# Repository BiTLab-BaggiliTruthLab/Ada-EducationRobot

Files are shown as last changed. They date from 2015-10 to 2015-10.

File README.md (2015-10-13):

# Ada-EducationRobot
######Ada the Cyber Security Awareness Robot
---
<a href="http://www.youtube.com/watch?feature=player_embedded&v=IIVzHWTThcU
" target="_blank">Ada The Cyber Security Education Robot</a>

## Building Instructions
---
###Hardware
Hardware building instructions can be found in our <a href="http://www.unhcfreg.com/#!Ada-The-Cyber-Security-Education-Robot/c5rt/561c4c410cf297bd6860a78e">blog post</a>

###Software
The code for the master and slave applications can be found in /Ada-EducationRobot/SecuroBotMaster and /Ada-EducationRobot/SecuroBotSlave, respectively. These folders can be imported into Android Studio. Android Studio is a free program that can be downloaded <a
href="http://developer.android.com/sdk/index.html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">here</a>.

The Arduino code can be found in /Ada-EducationRobot/SecuroBotServo/SecuroBotServo.ino. This code can be opened in the Arduino IDE, downloadable from <a
href="https://www.arduino.cc/en/Main/Software">here</a>.

##Contact
##### Made by Devon Clark
dclar4@unh.newhaven.edu

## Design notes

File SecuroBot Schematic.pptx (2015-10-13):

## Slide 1

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
TIP31

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
Slave
Audio
Out

L

R

●

+
LM324

GND

V+

47kΩ

+5V

IR Sen.

SIG

GND

4.7kΩ

●

●

●

●

+5V

Servo

GND

SIG

G5V-2-H1 5V Relay

●

●

330Ω

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
Master Tablet USB

Vcc

GND

●

D+

D-

Slave Tablet USB

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
LM7805

3

2

●

1

LM7805

3

2

1

LM7805

3

2

Android IOIO

13

9

1N4007

●

●

1N4007

●

●

●

VIN

GND

+5V

0 (Rx)

Arduino

7

9

7.4VDC
5000mAh

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
LEADS

VIN

●

●

●

1N4007

●

●

●

1N4007

●

●

●

●

GND

●

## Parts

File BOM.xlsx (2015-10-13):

Description | Pkg QTY | QTY of Pkgs | Used QTY | Pkg Cost | Unit Cost | Used Cost | Link
Battery | 1 | 2 | 2 | $18.40 | $18.40 | $36.80 | http://www.ebay.com/itm/RC-Turnigy-5000mAh-2S-20C-Lipo-Pack-/261569382452?pt=LH_DefaultDomain_0
IR prox sensors (5V) w/cable | 1 | 1 | 1 | $13.95 | $13.95 | $13.95 | http://www.ebay.com/itm/1x-Sharp-GP2Y0A21YK0F-Infrared-IR-Distance-Sensor-10-80cm-/141429691827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
Android IOIO OTG (5-15V) | 1 | 1 | 1 | $39.95 | $39.95 | $39.95 | http://www.ebay.com/itm/SparkFun-IOIO-OTG-/191528032653?pt=LH_DefaultDomain_0&hash=item2c97f5d98d
90 deg audio cable - 4ft | 1 | 1 | 1 | $4.68 | $4.68 | $4.68 | http://www.ebay.com/itm/Sirius-XM-3-5mm-male-to-male-Auxiliary-Audio-Cable-Right-Angle-90-degrees-10065x-/221586020592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
90 deg micro USB cable | 1 | 2 | 2 | $2.39 | $2.39 | $4.78 | http://www.ebay.com/itm/StarTech-com-Micro-USB-Cable-A-to-Right-Angle-Micro-B-UUSBHAUB3RA-New-/281528968323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
amplified speaker system (5V) | 1 | 1 | 1 | $16.95 | $16.95 | $16.95 | http://www.ebay.com/itm/Frisby-Desktop-Laptop-Notebook-Computer-PC-Mini-USB-Powered-Portable-Speakers-/131376665293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
Standard Servo (5V) | 1 | 1 | 1 | $14.99 | $14.99 | $14.99 | http://www.radioshack.com/radioshack-standard-servo/2730766.html
Servo driven rotating base | 1 | 1 | 1 | 19.95 | $19.95 | $19.95 | http://www.robotshop.com/en/lynxmotion-base-rotate-kit-no-servo.html
5mm Blue LED | 1 | 12 | 12 | $0.49 | $0.49 | $5.88 | http://www.ledsupply.com/leds/5mm-led-blue-470nm-30-degree-viewing-angle
USB BLE transeiver (non hub) | 1 | 1 | 1 | $4.99 | $4.99 | $4.99 | http://www.dx.com/p/ultra-mini-bluetooth-3-0-usb-dongle-65631#.VhaAQflVhBc
proto board | 1 | 1 | 1 | $19.95 | $19.95 | $19.95 | http://www.adafruit.com/products/590
9 pin screw terminal | 1 | 3 | 3 | $3.05 | $3.05 | $9.15 | http://www.adafruit.com/product/2134
Arduino Uno | 1 | 1 | 1 | $24.95 | $24.95 | $24.95 | http://www.adafruit.com/product/50
SKYRC iMAX B6AC V2 battery charger | 1 | 1 | 1 | 55.99 | $55.99 | $55.99 | http://www.amazon.com/Genuine-SKYRC-Power-6Amps-50Watts/dp/B00ND7J38C
3 pin JST-XH balancer connectors | 10 | 1 | 1 | $2.74 | 0.274 | $0.27 | http://www.amazon.com/10pcs-JST-XH-Lipo-Balance-Extension/dp/B008TKMC86
male/female T style connectors | 10 | 1 | 1 | $3.10 | $0.31 | $0.31 | http://www.amazon.com/gp/product/B0070RS7V0?redirect=true
Battery socket and pin pair | 2 | 1 | 1 | $4.55 | $2.27 | $2.27 | http://www.amazon.com/Redcat-Racing-Banana-Version-Female/dp/B00D25G2HA
5V Voltage regulator LM1085 | 1 | 2 | 2 | $2.06 | $2.06 | $4.12 | http://www.mouser.com/ProductDetail/Texas-Instruments/LM1085IT-ADJ-NOPB/?qs=sGAEpiMZZMvu8NZDyZ4K0VV0B0ysNg0m
LM324 Quad Opperational Amplifier | 1 | 1 | 1 | $0.51 | $0.51 | $0.51 | http://www.mouser.com/ProductDetail/Fairchild-Semiconductor/LM324N/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
TIP31 NPN Transistor | 1 | 1 | 1 | $1.13 | $1.13 | $1.13 | http://www.mouser.com/ProductDetail/Central-Semiconductor/TIP31/?qs=sGAEpiMZZMutncetXCRkfnN4f3PuPq4Y
4.7kΩ Resistor | 1 | 1 | 1 | $0.70 | $0.70 | $0.70 | http://www.mouser.com/ProductDetail/Ohmite/OD472JE/?qs=sGAEpiMZZMuDPtTs5Gda20wkUEoAUy6cJVhknFF6uiU%3d
47kΩ Resistor | 1 | 1 | 1 | $0.70 | $0.70 | $0.70 | http://www.mouser.com/ProductDetail/Ohmite/OD473JE/?qs=sGAEpiMZZMuDPtTs5Gda2xA0s8Om0erSLiRj1MkjNK8%3d
330Ω Resistor | 1 | 1 | 1 | $0.70 | $0.70 | $0.70 | http://www.mouser.com/ProductDetail/Ohmite/OD331JE/?qs=sGAEpiMZZMuDPtTs5Gda29oHdSiM7txmqu9ayzW2Kb0%3d
G5V-2-H1 5V Relay | 1 | 1 | 1 | $2.99 | $2.99 | $2.99 | http://www.mouser.com/ProductDetail/Omron-Electronics/G5V-2-H1-DC5/
DPST toggle switch (center off) | 1 | 1 | 1 | $5.99 | $5.99 | $5.99 | http://www.mouser.com/ProductDetail/NKK-Switches/S7A/
heat sink | 1 | 2 | 2 | $0.51 | $0.51 | $1.02 | http://www.mouser.com/ProductDetail/Aavid-Thermalloy/576802B04000G/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
1N4007 Diode | 1 | 2 | 2 | $0.18 | $0.18 | $0.36 | http://www.mouser.com/ProductDetail/Fairchild-Semiconductor/1N4007/?qs=sGAEpiMZZMuQUXCJI7Y4lvWy%252b1U8RtCq
*80/20 1.5in. solid extrusion - 8ft | 1 | 2 | 1.5 | $61.31 | $61.31 | $91.97 | http://www.mcmaster.com/#47065t103/=wu75em
80/20 1.5in 90 deg corner | 1 | 0 | 0 | $7.84 | $7.84 | $0.00 | http://www.mcmaster.com/#47065t243/=wu7542
80/20 1.5in 90 deg brace | 1 | 5 | 5 | $7.98 | $7.98 | $39.90 | http://www.mcmaster.com/#5537t51/=wu75yk
grey wire track snap (6ft length) | 1 | 1 | 1 | $4.27 | $4.27 | $4.27 | http://www.mcmaster.com/#47065t4/=z9058j
5/16 Aluminum washers | 100 | 1 | 22 | $7.88 | $0.08 | $1.73 | http://www.mcmaster.com/#93286a015/=z945r5
7" x 5" x 2.5" Electrical enclosure | 1 | 1 | 1 | $12.20 | $12.20 | $12.20 | http://www.mcmaster.com/#7593k32/=z90j3c
80/20 T-slot fastener for 1.5 in. extrusion | 4 | 5 | 18 | $2.71 | $0.68 | $12.20 | http://www.mcmaster.com/#47065t97/=z621i9
1.75 X 5/16-18 socket head cap screw | 2 | 1 | 2 | $2.10 | $1.05 | $2.10 | http://www.homedepot.com/p/Crown-Bolt-5-16-in-x-1-3-4-in-Internal-Hex-Socket-Cap-Head-Cap-Screws-2-Pack-45338/203576071
5/16 - 18 1.25 in. bolt | 1 | 2 | 2 | $0.20 | $0.20 | $0.40 | http://www.lowes.com/pd_63318-37672-190096_1z0v10o__?productId=3058581&pl=1
1/2in conduit strain relief | 1 | 3 | 3 | $3.04 | $3.04 | $9.12 | http://www.lowes.com/pd_108659-15527-49212___?productId=3150213&pl=1&Ntt=gampak+flex+connector
1/2in conduit lock nut | 2 | 2 | 3 | $1.50 | $0.75 | $2.25 | http://www.lowes.com/pd_75927-15527-47106_1z0xc72__?productId=1100417&pl=1
#6-32 X 1.5 in. machine screw/nut | 10 | 1 | 2 | $1.24 | $0.12 | $0.25 | http://www.lowes.com/ProductDisplay?productId=3035920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
.25x.14x1 in. nylon spacers | 2 | 1 | 2 | $0.56 | $0.28 | $0.56 | http://www.lowes.com/pd_136921-37672-880429_0__?productId=3012432
#6-32 x 1.25 machine screw/nut | 10 | 1 | 8 | $1.24 | $0.12 | $0.99 | http://www.lowes.com/pd_57834-37672-605399___?productId=4746423&pl=1&Ntt=57834
#4-40 x 0.5in machine screw | 8 | 1 | 6 | $1.24 | $0.15 | $0.93 | http://www.lowes.com/pd_62179-37672-605438_0__?productId=4746589
2" grey swivel wheel w/lock | 1 | 4 | 4 | $4.97 | $4.97 | $19.88 | http://www.lowes.com/pd_235514-255-4031299NN_0__?productId=3026956
5/16 lock washers | 1 | 20 | 20 | $0.18 | $0.18 | $3.60 | http://www.lowes.com/pd_63409-37672-300021___?productId=3036826&pl=1&Ntt=5%2F16+lock+washer
3/8 lock washer | 1 | 4 | 4 | $0.23 | $0.23 | $0.92 | http://www.lowes.com/pd_61816-37672-811056___?productId=3036632&pl=1&Ntt=3%2F8+lock+washer
3/8 - 16 nut | 1 | 8 | 8 | $0.22 | $0.22 | $1.76 | http://www.lowes.com/pd_63303-37672-150009_4294856646+5003696+4294838133_4294937087?productId=3058551
#10-32 X 1/2" machine screw w/ nut | 10 | 1 | 3 | $1.24 | $0.12 | $0.37 | http://www.lowes.com/pd_57851-37672-491306___?productId=3035878&pl=1&Ntt=%2310-32+x+1%2F2
#10 lock washer | 48 | 1 | 3 | $1.24 | $0.03 | $0.08 | http://www.lowes.com/pd_58135-37672-490694___?productId=3035994&pl=1&Ntt=%2310+lock+washer
#6 x 0.5-in Stainless Steel Screws | 12 | 1 | 8 | $1.54 | $0.13 | $1.03 | http://www.lowes.com/pd_329037-37672-126976___?Ntt=126976&UserSearch=126976&productId=3818121
Nexus 7 tablet | 1 | 2 | 2 | 149 | $149.00 | $298.00 | http://www.newegg.com/Product/Product.aspx?Item=N82E16834231150&cm_re=nexus_7-_-34-231-150-_-Product
 |  |  |  |  | Total: | $798.54 | *This does not include the cost of filiment for 3D printing or wire

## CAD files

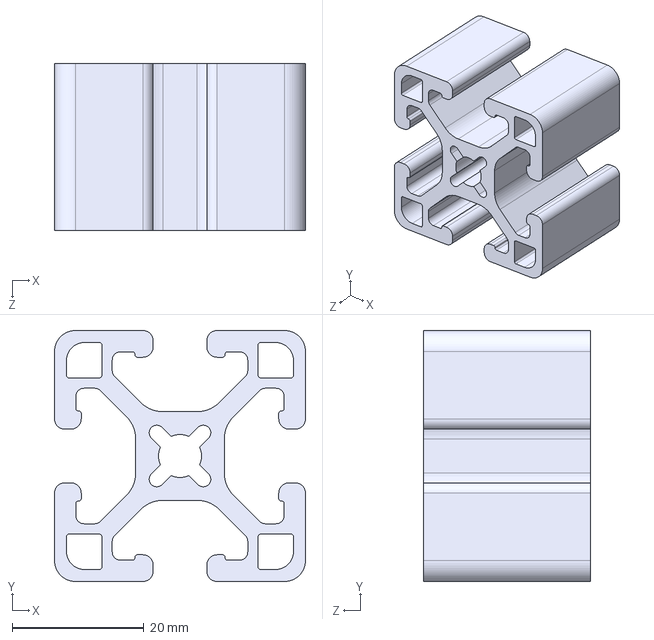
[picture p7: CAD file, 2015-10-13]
SecuroBot Hardware Files/CAD Files/Imported Components/8020 - extrusion - 1 inch/1 inch extrusion base.step
38.1 x 38.1 x 25.4 mm

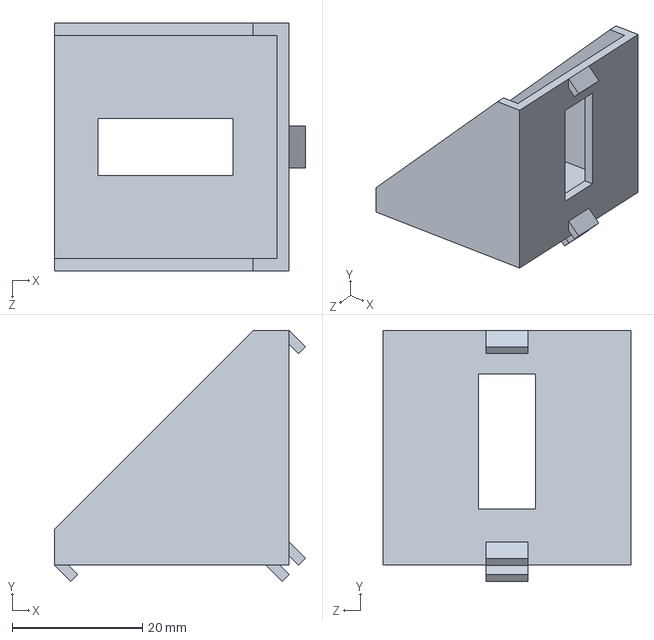
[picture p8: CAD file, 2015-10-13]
SecuroBot Hardware Files/CAD Files/Imported Components/ANGLE BRACE/ANGLE BRACE.STEP
38.5 x 38.5 x 38.0 mm

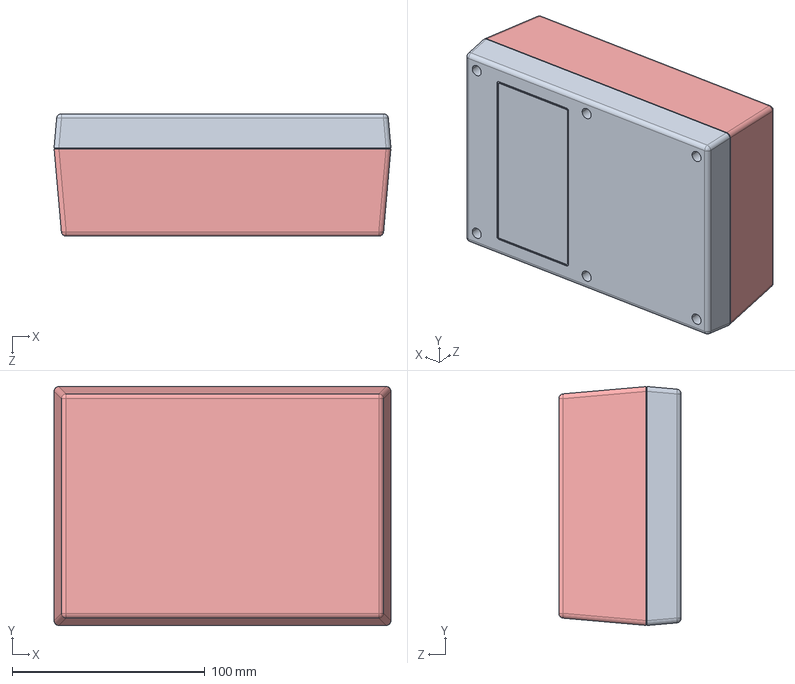
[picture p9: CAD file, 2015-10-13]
SecuroBot Hardware Files/CAD Files/Imported Components/enclosure/enclosure.STEP
174.8 x 124.0 x 63.5 mm

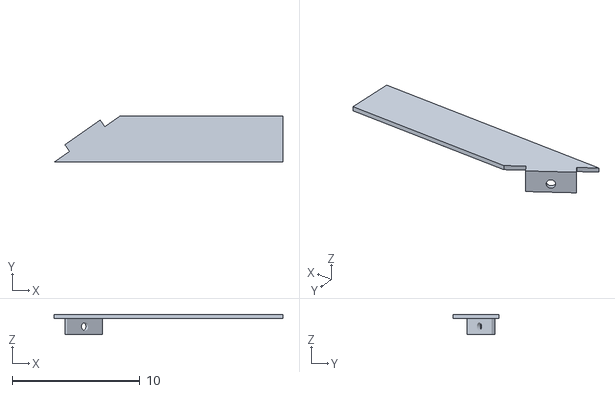
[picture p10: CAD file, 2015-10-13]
SecuroBot Hardware Files/STL Files/Right Forearm.stl
17.9 x 3.64 x 1.59

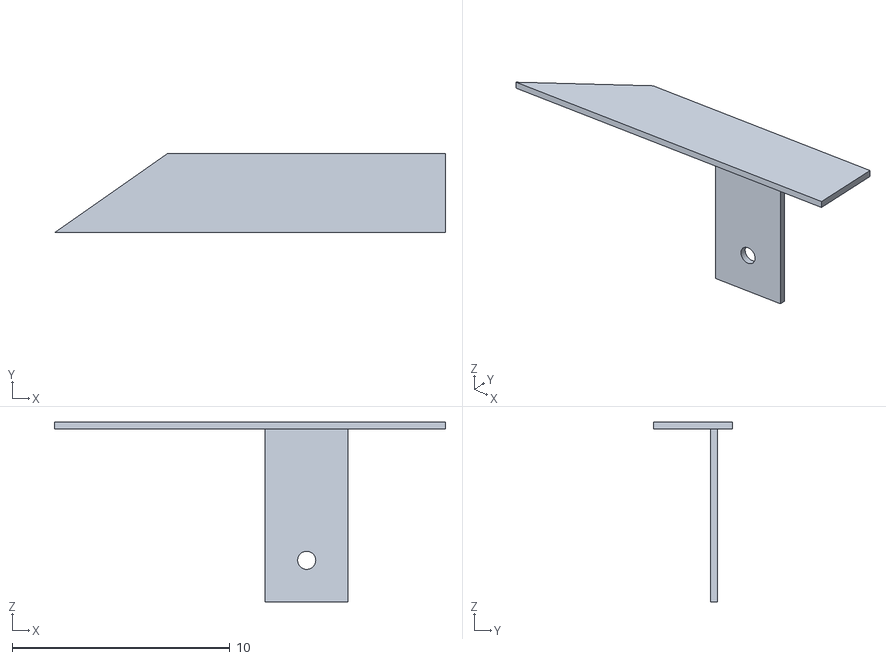
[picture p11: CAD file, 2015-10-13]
SecuroBot Hardware Files/STL Files/Left Forearm.stl
17.9 x 3.64 x 8.24

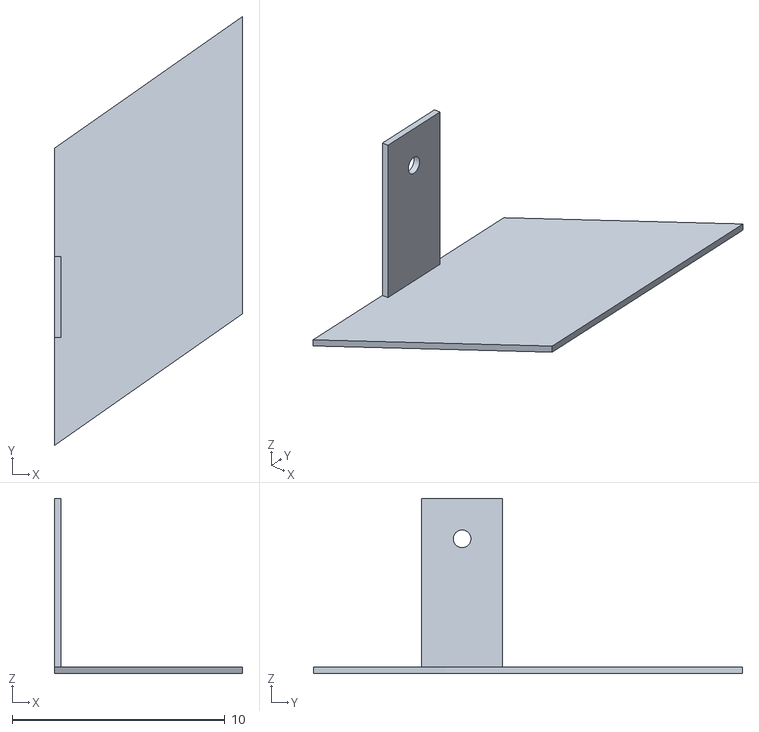
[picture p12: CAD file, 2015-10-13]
SecuroBot Hardware Files/STL Files/Right Abdomen.stl
8.84 x 20.2 x 8.24

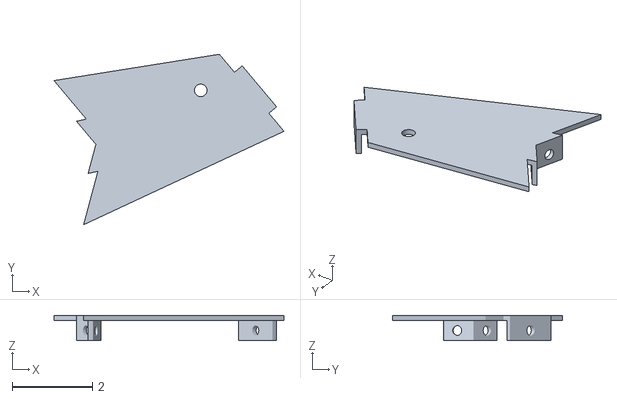
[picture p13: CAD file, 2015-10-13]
SecuroBot Hardware Files/STL Files/Right Bicep.stl
5.72 x 4.24 x 0.625

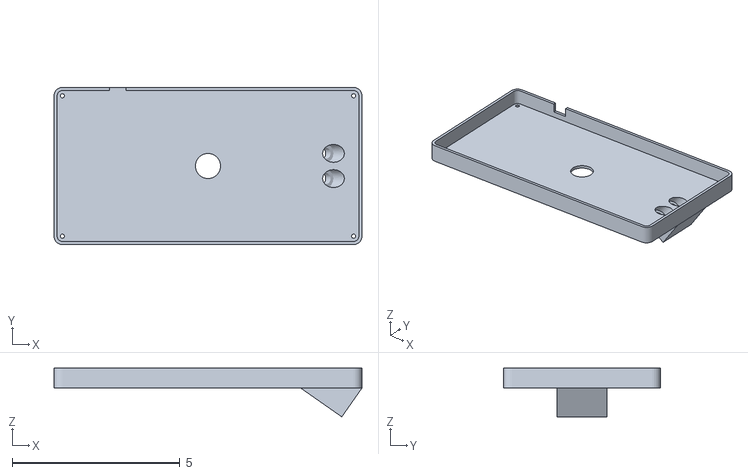
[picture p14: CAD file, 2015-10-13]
SecuroBot Hardware Files/STL Files/Slave Tablet Enclosure.stl
9.19 x 4.69 x 1.45

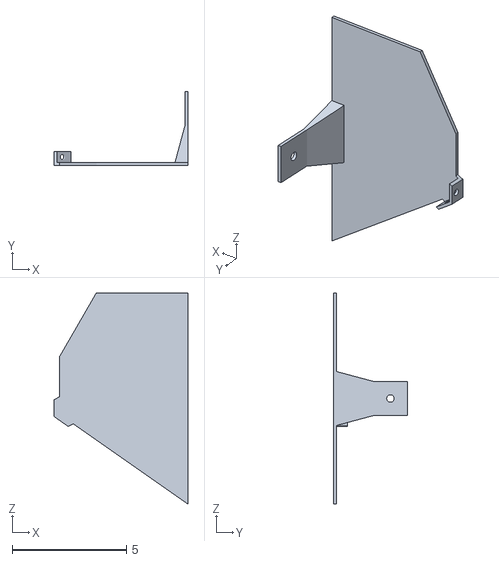
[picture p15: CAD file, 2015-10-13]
SecuroBot Hardware Files/STL Files/Right Chest.stl
5.85 x 3.25 x 9.25

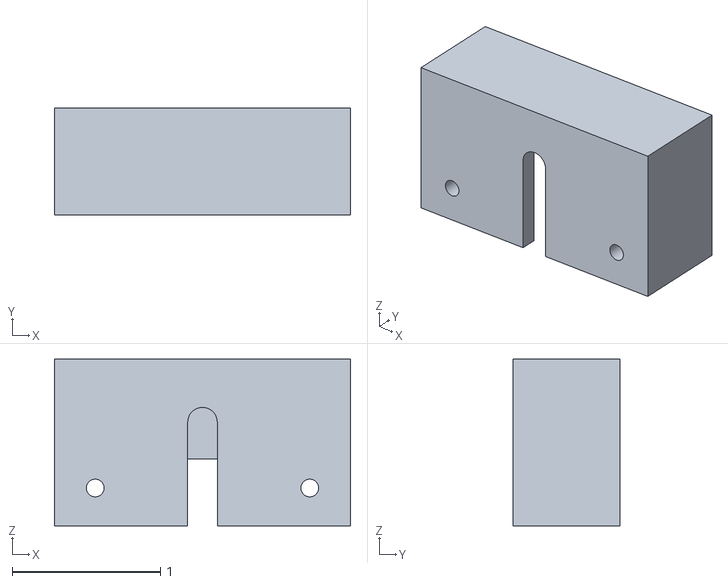
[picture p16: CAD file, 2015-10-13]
SecuroBot Hardware Files/STL Files/IR Cover.stl
2.00 x 0.725 x 1.12

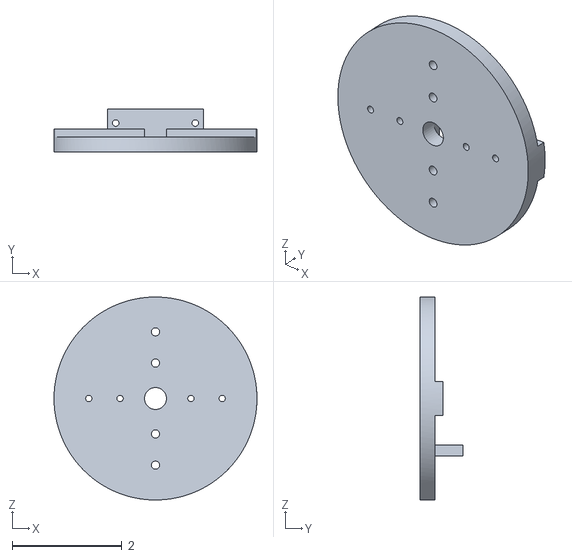
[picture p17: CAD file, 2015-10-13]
SecuroBot Hardware Files/STL Files/Master Tablet and IR Mount.stl
3.70 x 0.78 x 3.70

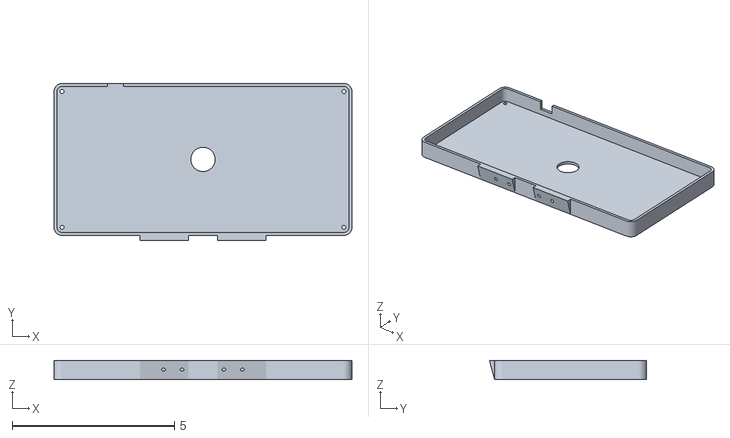
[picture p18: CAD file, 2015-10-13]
SecuroBot Hardware Files/STL Files/Master Tablet Enclosure.stl
9.19 x 4.85 x 0.594

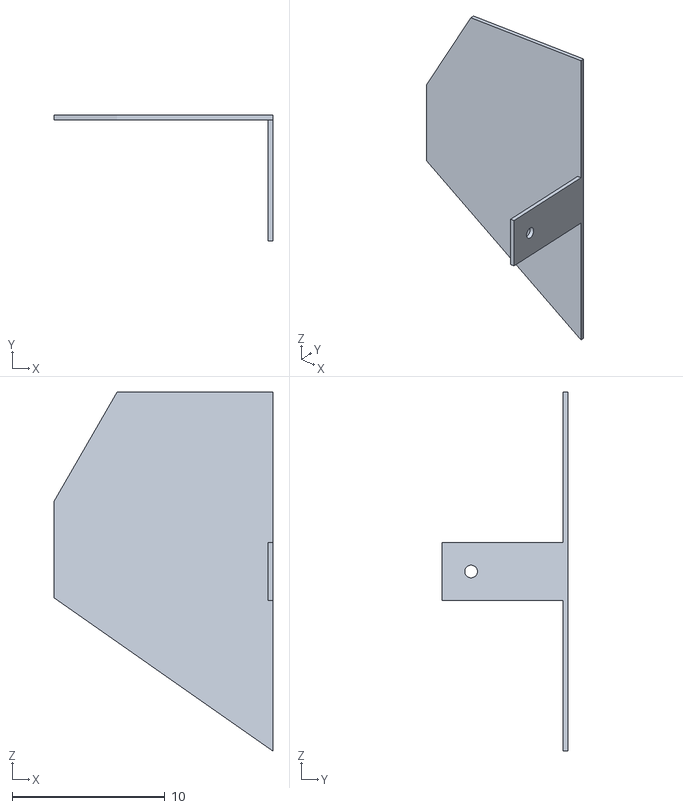
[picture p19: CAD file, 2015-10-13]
SecuroBot Hardware Files/STL Files/Left Chest.stl
14.3 x 8.24 x 23.5

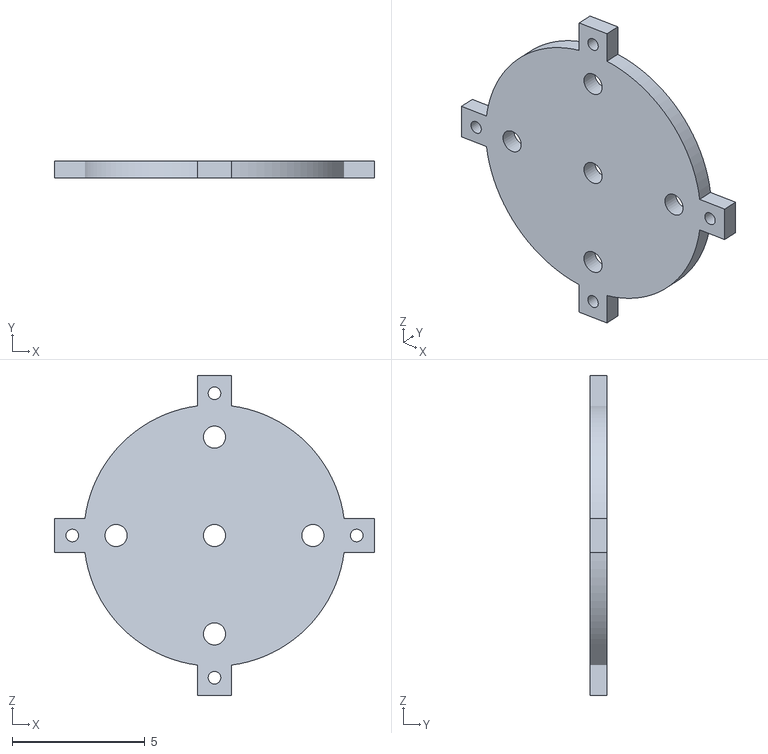
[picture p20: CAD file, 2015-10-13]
SecuroBot Hardware Files/STL Files/Rotating Base mount.stl
12.0 x 0.635 x 12.0

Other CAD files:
SecuroBot Hardware Files/STL Files/Left Abdomen.stl
SecuroBot Hardware Files/STL Files/Chest Standoff.stl
SecuroBot Hardware Files/STL Files/Left Bicep.stl
SecuroBot Hardware Files/CAD Files/3D Printed Parts/Chest Standoff.ipt
SecuroBot Hardware Files/CAD Files/3D Printed Parts/IR Cover.ipt
SecuroBot Hardware Files/CAD Files/3D Printed Parts/Left Abdomen.ipt
SecuroBot Hardware Files/CAD Files/3D Printed Parts/Left Bicep.ipt
SecuroBot Hardware Files/CAD Files/3D Printed Parts/Left Chest.ipt
SecuroBot Hardware Files/CAD Files/3D Printed Parts/Left Forearm.ipt
SecuroBot Hardware Files/CAD Files/3D Printed Parts/Left Hip.ipt
SecuroBot Hardware Files/CAD Files/3D Printed Parts/Master Tablet Cover.ipt
SecuroBot Hardware Files/CAD Files/3D Printed Parts/Master Tablet Enclosure.ipt
SecuroBot Hardware Files/CAD Files/3D Printed Parts/Master Tablet and IR Mount.ipt
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

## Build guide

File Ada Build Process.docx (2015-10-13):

# Introduction

Ada is an open source project initiated by the University of New Haven Cyber Forensics Research and Education Group (UNHcFREG). Ada was designed to provide users with valuable cyber security tips and information in a way that is both interactive and entertaining. Ada is capable of reading tweets, checking if email accounts have been hacked, reading RSS feeds, providing tips, prompting quizzes, telling jokes, and showing articles – all related to cyber security. It is our hope that people will take advantage of the open source nature of this project to build Ada for use in their own schools and universities and contribute to the project to make Ada better.

Ada has three major components – Mechanical, Electrical, and Software. The mechanical components were designed using AutoDesk Inventor 2014, several of which were 3D printed using a MakerBot Replicator 5th Generation and a Stratasys Dimension 3D printer. The electrical design was done by hand with good ole’ pencil and paper. The software components were made using a few different programs. Two separate Android applications were designed using Android Studio, these are SecuroBotMaster and SecuroBotSlave. The master app acts as Ada’s software eyes. The slave app is responsible for fetching and running all of the content as well as interfacing with the hardware to move the head and handle the communication and interaction with the user. The on board Arduino is running a program that was written using the Arduino IDE. This program is used to interface with the servo which controls the head movement. Table 1 below outlines the bill of materials for all parts used to create Ada.

Table 1 – Ada’s complete bill of materials.

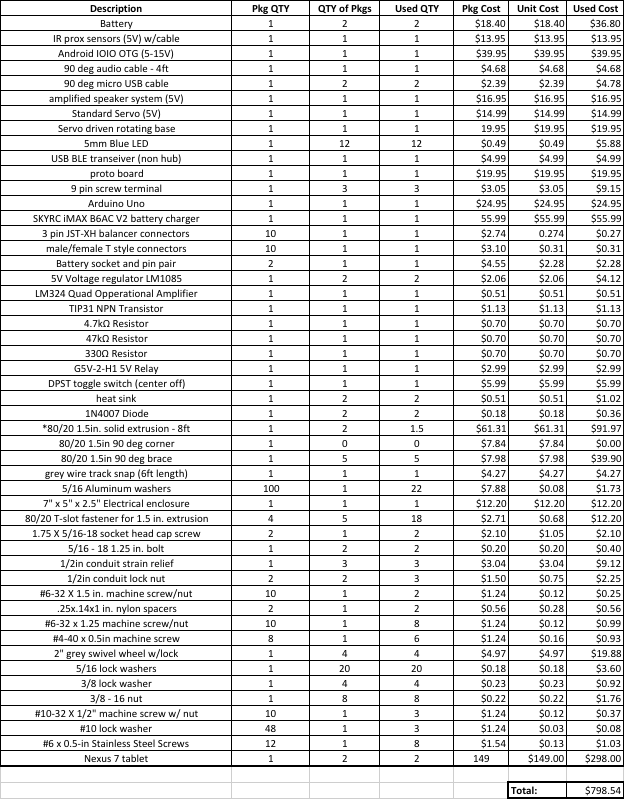
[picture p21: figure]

The following provides a basic instructional guide for how you can build your very own Ada. All software, CAD, bill of materials, schematics, and other relevant documentation is available for download by following this link:

https://github.com/unhcfreg/Ada-EducationRobot

We hope you decide to build your own Ada and look forward to Ada’s future!

# Procedure

The following outlines the procedure for constructing Ada. It is separated into three main sections – Mechanical, Electrical, and Software. Ada is capable of running on as little hardware as just a tablet. Therefore, it is up to you as the builder to decide what other features you would like to include. Our version of Ada is stationary but animatronic. Her head moves but the body stays still. She also has an onboard speaker system with a light that blinks to the sound of her voice. We have integrated a 5000mAh battery into our model which is enough to keep the system running as well as charge the tablets for several hours. Feel free to add or subtract components as you wish! The following procedure assumes you have obtained all of the items outlined in the bill of materials and have access to a basic tool set as well as a few more advanced tools such as a soldering iron, Bridgeport machining center, horizontal ban saw, and a medium to large sized 3D printer.

## Mechanical

As mentioned earlier, all of the CAD was designed in AutoDesk Inventor 2014 and is included in the download. We have included all of the .ipt files as well as the .stl files for those parts that are 3D printed. The fully assembled Ada can be seen in Fig. 1 below.

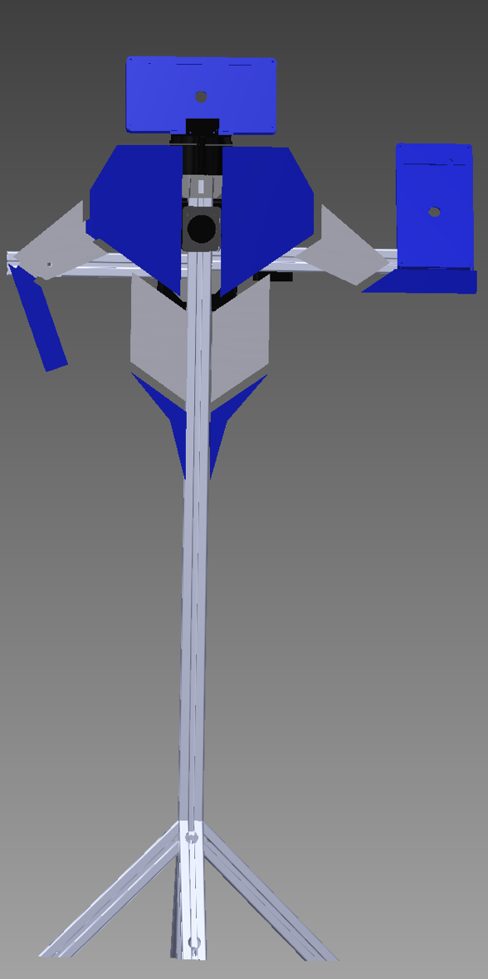
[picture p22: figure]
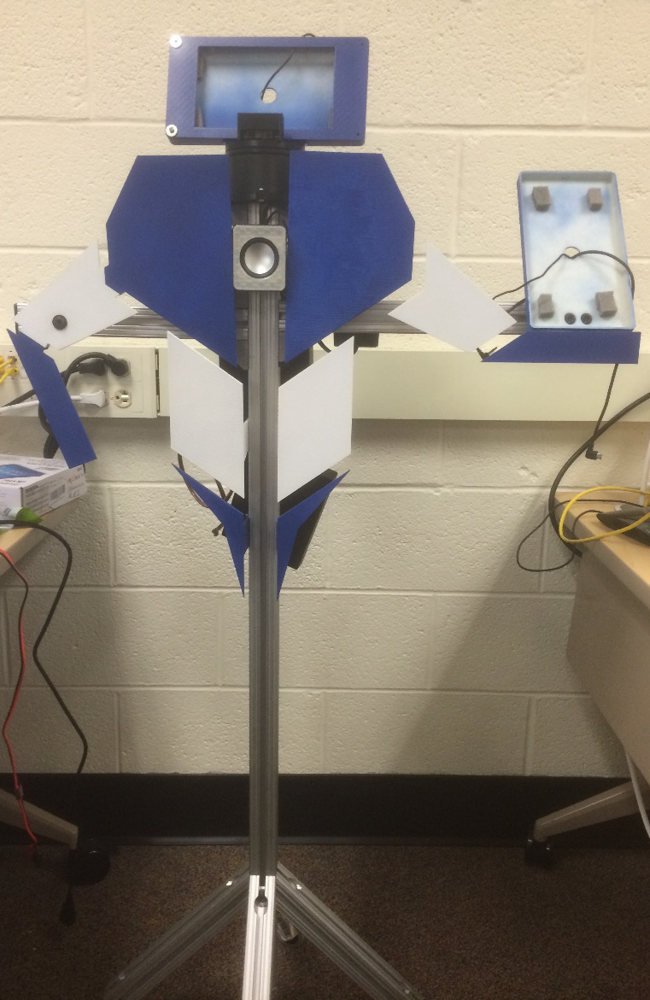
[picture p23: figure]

Figure 1 – Ada fully assembled.

The first step in building Ada is to construct the frame. The frame is the rigid aluminum structure that holds all of the other components. The frame components are located in a folder called “Milled Extrusion Parts”. This frame was constructed out of 1.5in. 80/20 aluminum extrusion. The extrusion was cut to rough length with a horizontal ban saw and was then milled to exact length using a Bridgeport machining center. It is possible to skip this last step but it will leave the edges in rough shape and the parts may not line up perfectly square. Once all the pieces are cut, they are assembled using the 80/20 T-slot fasteners and the angle braces. The fully assembled frame can be seen below in Fig. 2.

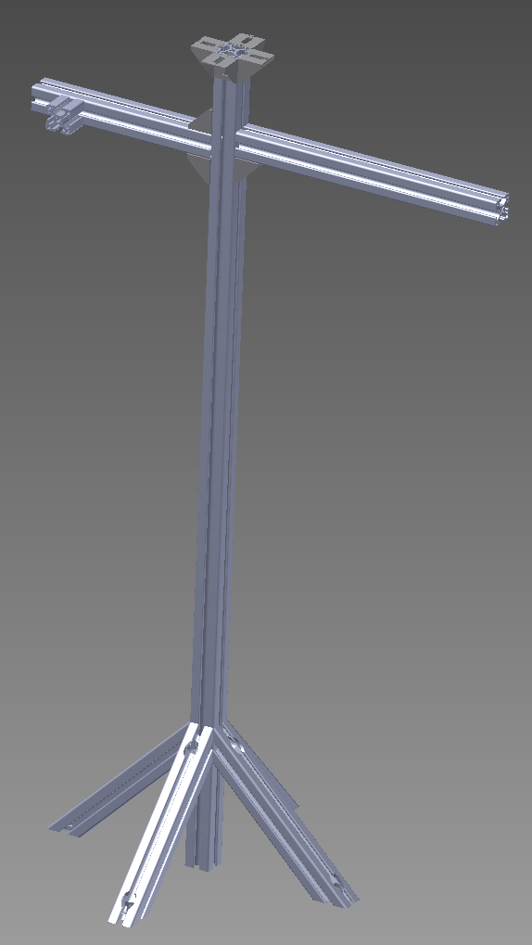
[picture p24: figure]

Figure 2 - Ada’s frame constructed of 80/20 extrusion.

The next step was to print all of the pieces in the “3D Printed Parts” folder. Two different 3D printers were used to print these parts – A MakerBot Replicator 5th Generation and a Stratasys Dimension 3D printer. The Dimension was the preferred printer for most of these parts, however both have their advantages and disadvantages in printing these parts. The Dimension was able to print the bigger parts much better. This is because of the climate controlled environment, not available in the MakerBot. The Dimension was also much better equipped to print more complex parts due to the nature of its build process. The Dimension actually builds a dissolvable support layer which holds parts together that would otherwise not be able to support themselves on their own during the build process. These supports do however come at a cost. The cost being time and money. It is much more expensive to run this printer and cost more because of the material. The MakerBot was used to print small parts much faster and cheaper than the Dimension. Parts such as the speaker cover, stand offs, rotating base mount, and other small parts were all printed using the MakerBot. We found that the MakerBot could not print the larger pieces such as the chest plates, because the material would peel off the build surface while being printed. Parts that actually managed to stick to the surface would come out warped. This is most likely due to the lack of a climate controlled build environment. For our version of Ada, we decided to do most of the printing with a single color of filament (white) however a few parts were printed in other colors. The IR cover, Rotating Base Mount, and Master Tablet and IR Mount were all printed in black to match the rotating base. The Speaker Cover was printed using a translucent filament which allowed the light from the LEDs to be seen. The body parts were then spray painted in alternating blue and white, representing our school’s colors. It is recommended that you actually print the parts using the correct color filament, as it looks nicer in the end and you will save time by skipping the spray paint step. At this point, most of the body parts can be fastened to the frame, again using the T-slot fasteners. Ada’s Right chest, bicep, and forearm are fastened using #10-32 screws and nuts. At this point, Ada should start taking a recognizable shape as seen in Fig. 3.

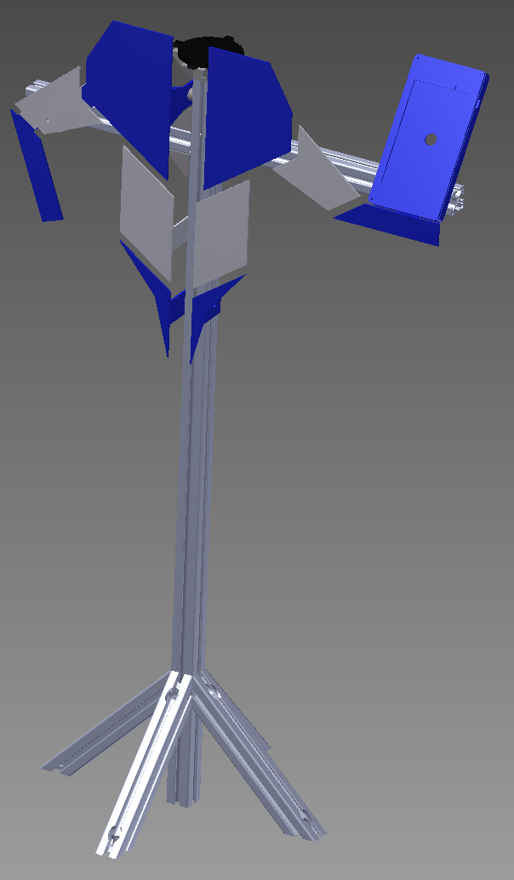
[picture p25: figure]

Figure 3 – Ada with most of her body parts mounted using T-slot fasteners.

The wheels are fastened to the legs using 3/8-16 bolts and 3/8 lock washers as seen in Fig. 4 below.

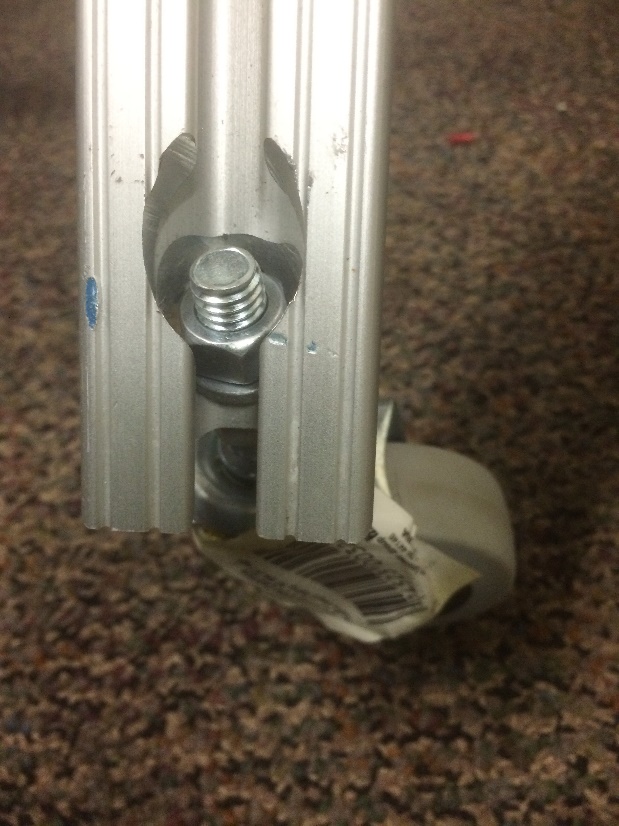
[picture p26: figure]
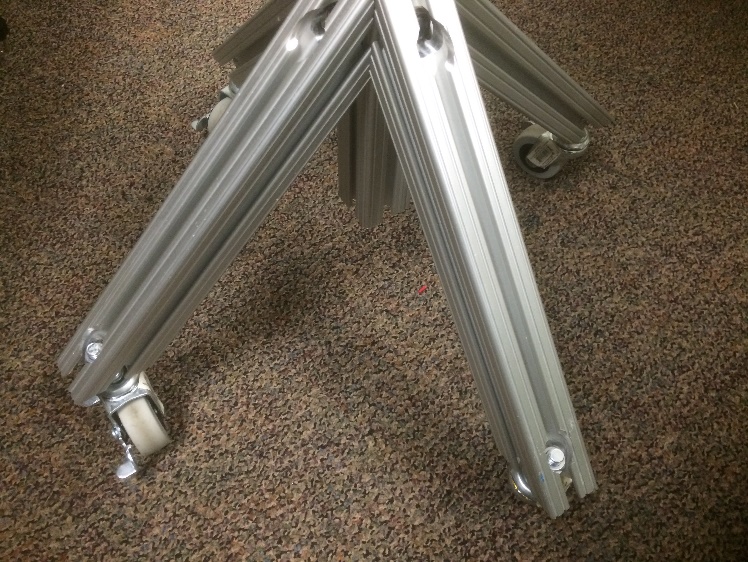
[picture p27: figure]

Figure 4 – Swivel wheels are mounted to Ada’s legs for easy transportation.

Next, the servo is fastened to the rotating base using the included hardware. Because of the way we have built our Master tablet mount, it is necessary to put washers under the servo before fastening it to the underside of the rotating base, seen below in Fig. 5.

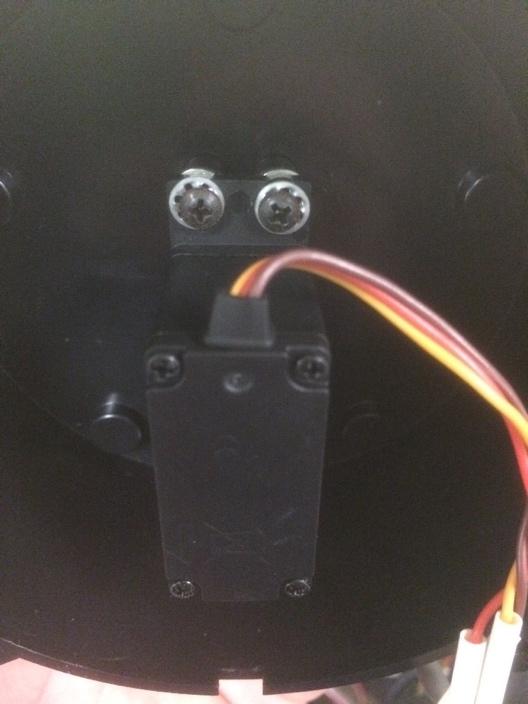
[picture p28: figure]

Figure 5 – Washers are placed under the servo before mounting.

With the rotating base assembled, the IR sensor can be screwed into place on the Master Tablet and IR Mount, along with the IR cover. The mounted IR sensor assembly is show in Fig. 6.

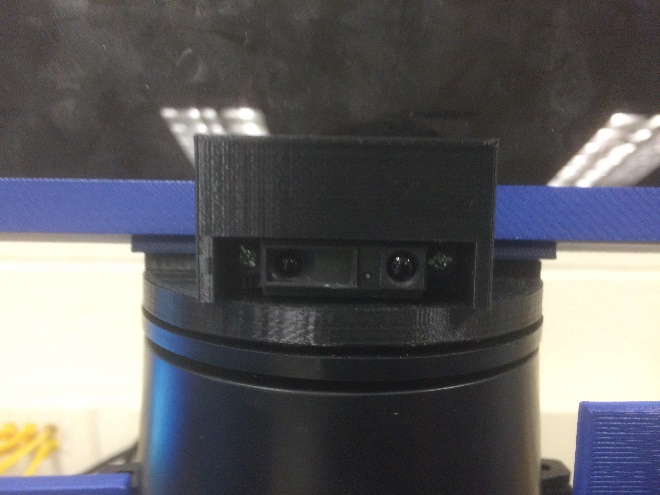
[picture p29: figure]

Figure 6 – The IR sensor is fastened to the mount.

After this, the speakers are mounted. 5/16 in. holes are drilled in each of the speaker heads in order to mount them to the frame using the T-slot fasteners (Fig. 7). Small pieces of foam can be hot glued to the tablet enclosures to keep the tablets firmly pressed against the cover and not shaking around (Fig. 8).

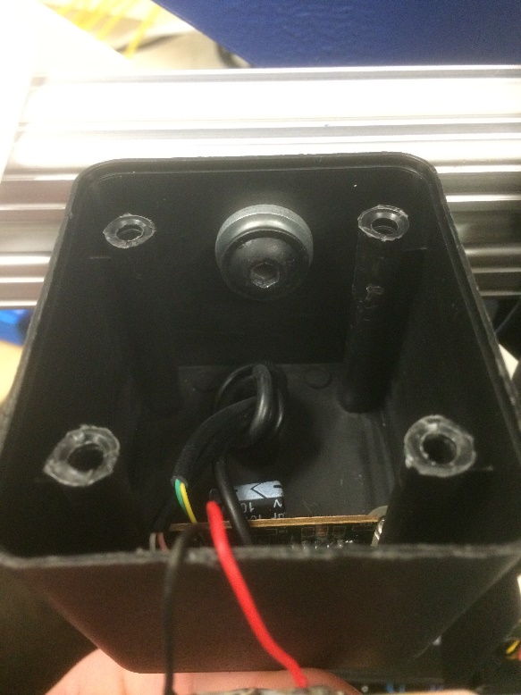
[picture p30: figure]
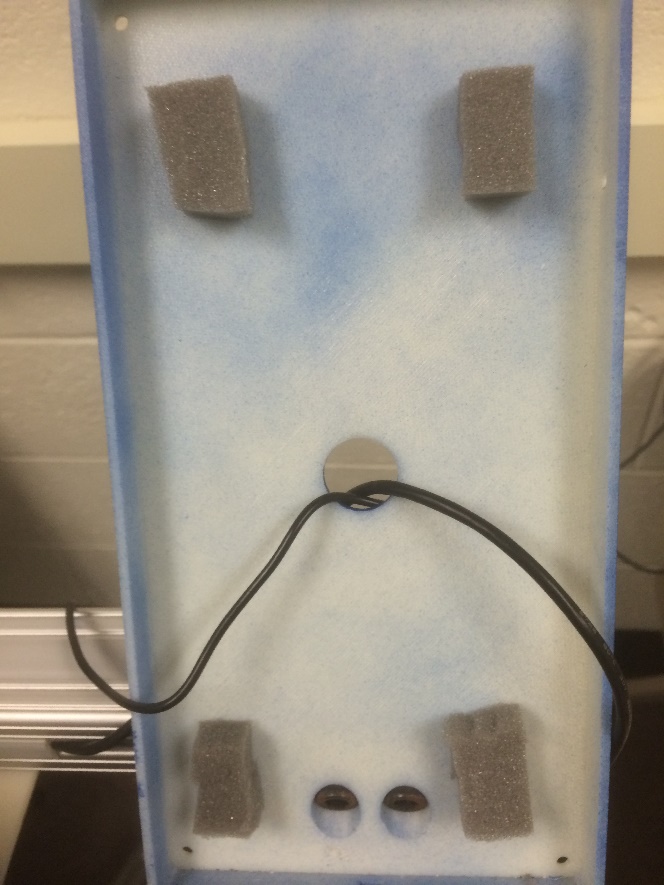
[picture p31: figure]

Figure 7 – Speakers mounted to frame. Figure 8 – Foam is added to tablet enclosures.

At this point, the master tablet enclosure can be fastened to the Master Tablet and IR Mount using #6 screws. The assembly now looks like Fig. 9.

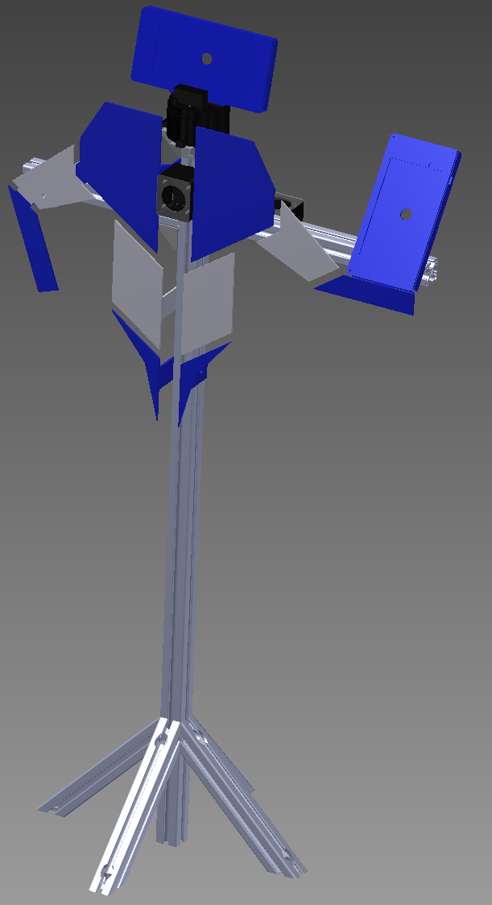
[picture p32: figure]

Figure 9 – All body parts attached, just missing the electrical enclosure.

The final stage of the mechanical assembly is to mount the electrical enclosure. Before this can be mounted however, a few holes need to be drilled. First, four holes are drilled in the top, right, and bottom sides of the enclosure. These holes are for 3 wire strain reliefs and the main power toggle switch. The next set of holes to be drilled are for the circuit board. Holes for the main board can be drilled through the back of the enclosure and holes for mounting the Arduino board can be drilled in the cover. It is our experience that this enclosure is pretty tight with everything in it, so you may want to invest in a slightly larger enclosure, especially if you plan on expanding more on the electronics. Finally, two 5/16 in. holes can be drilled in the back of the enclosure on vertical center for mounting to the frame. With all of this done, the enclosure can now be mounted to the frame using T-slot fasteners. Ada should now look like Fig. 10 from behind.

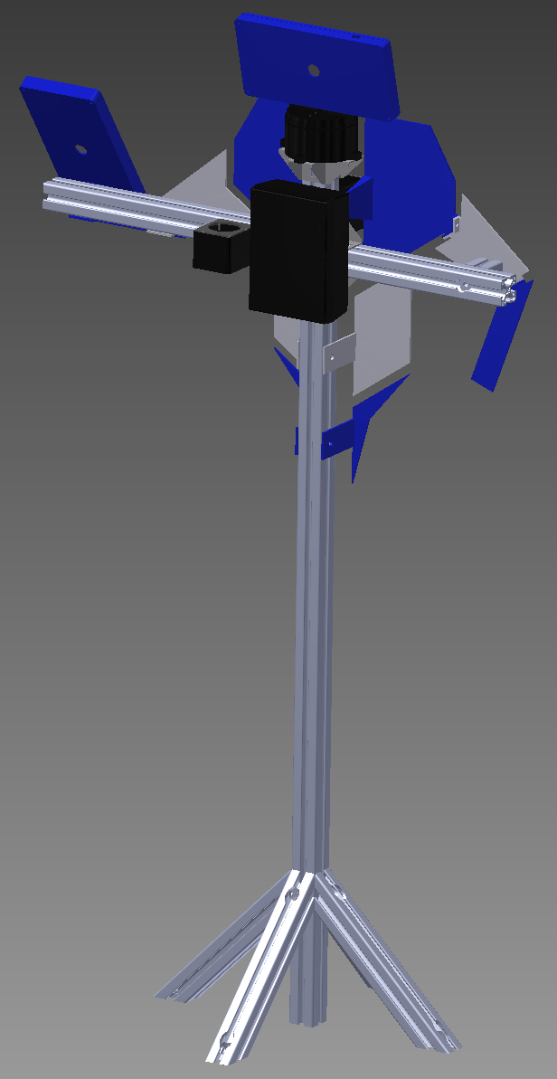
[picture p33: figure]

Figure 10 – Ada rear view. All components mounted.

## Electrical

With the mechanical components all in place, it is now time to being the electronic assembly. The schematic in Fig. 11 was created to assist in the wiring process.

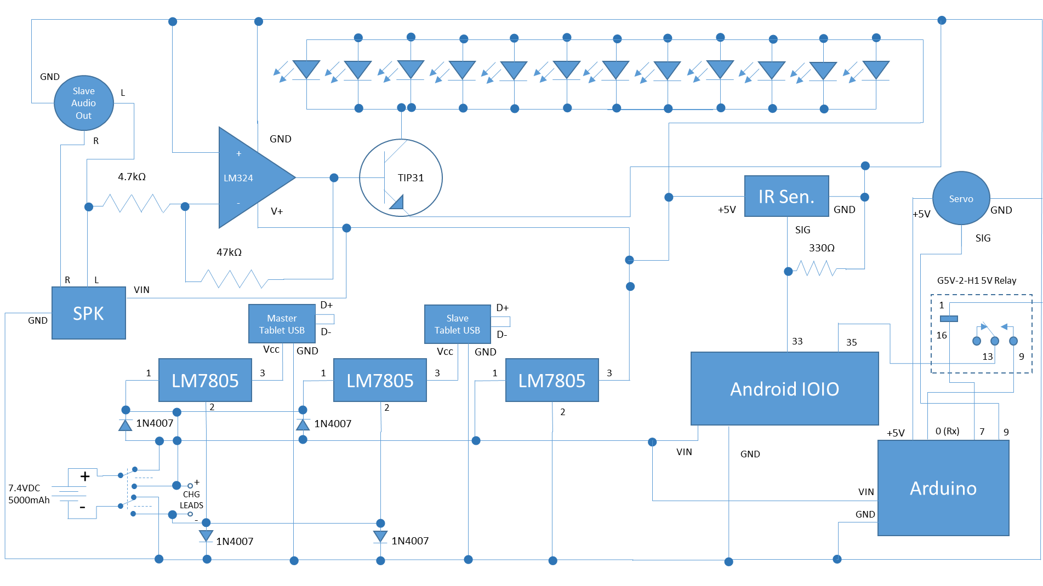
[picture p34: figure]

Figure 11 – Electrical schematic. Includes components internal and external to enclosure.

Most of these components reside on the main board, however there are many which reside elsewhere in the system. Components such as the servo, IR sensor, and speaker are mounted externally. Other items such as the relay, Arduino, and toggle switch are contained within the enclosure, just not on the main board. The mounting holes for these components were discussed in the previous section. With the above circuit in mind, the components were arranged on the proto-board for soldering. One way of doing this can be seen below in Fig. 12.

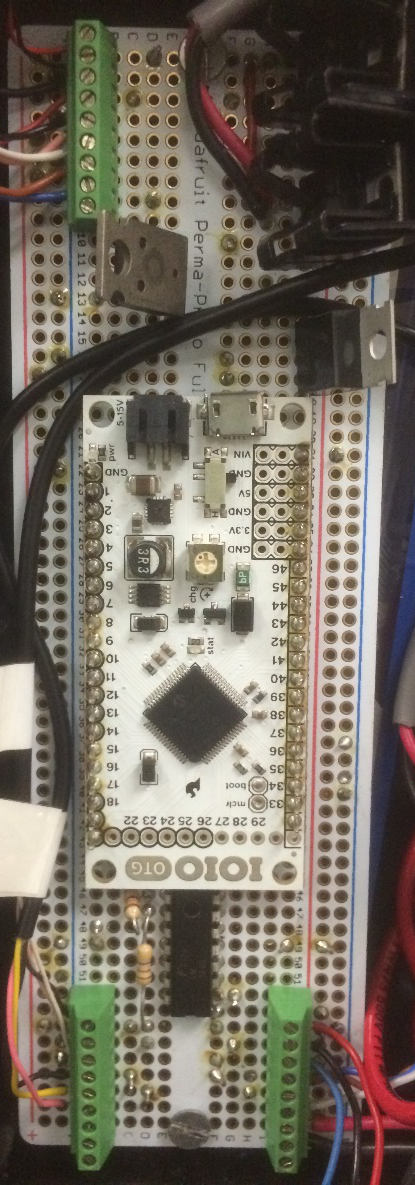
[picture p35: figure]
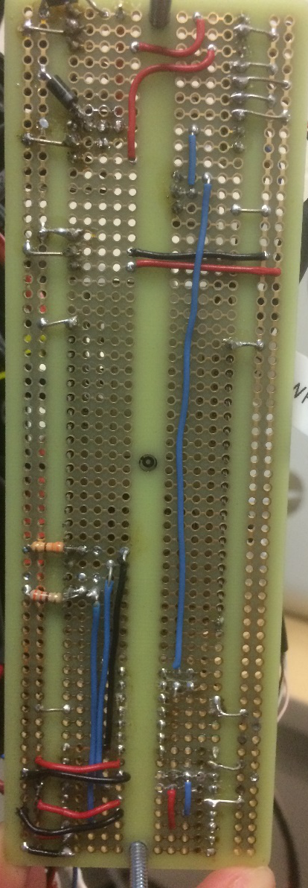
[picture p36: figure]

Figure 12 – Top and bottom views of the main circuit board.

Above is the configuration we have chosen to use, where the picture on the left shows the top of the board and the right shows the bottom. The picture on the right is a 180 deg. rotated view of the picture on the left. The green 9-pin screw terminals are used to connect external electronics to the board. Heat sinks are used on two out of the three LM7805 voltage regulators. These regulators are responsible for charging the tablets which can draw up to 0.75 Amps while charging, thus requiring heat dissipation via the heat sinks. Once this board has been assembled, it can be fastened to the inside of the enclosure. The battery should be first slipped in, and then the main PCB with 1.25 in. standoffs can be screwed into place. Next, the toggle switch, Arduino, and relay can be installed and wired. It should be noted that anything components that are in direct contact with the battery are wired using 14AWG wire, where as anything that is 5VDC and less is wired using 26AWG wire. The toggle switch, relay, and Arduino wiring can be seen below as seen below in Fig. 13 and 14.

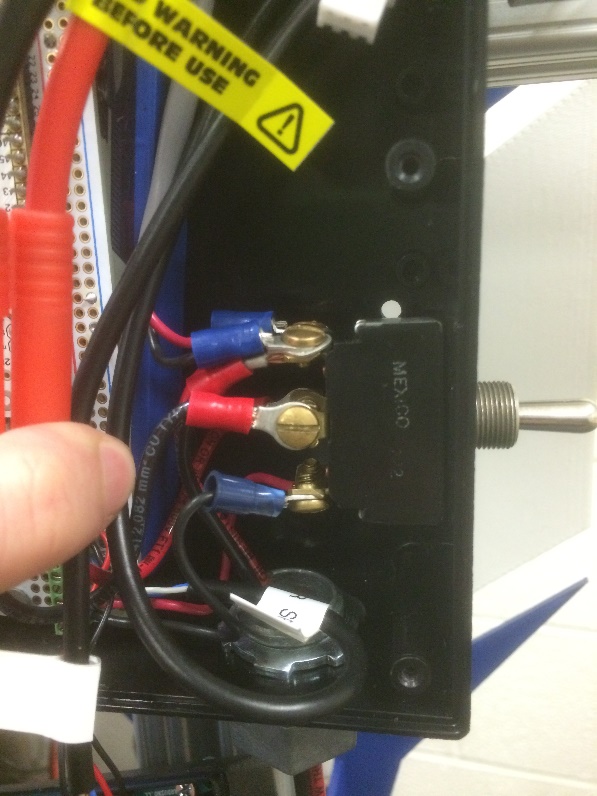
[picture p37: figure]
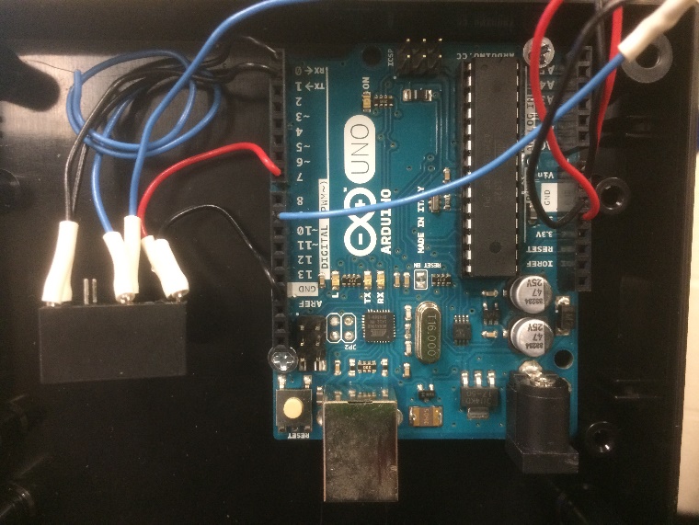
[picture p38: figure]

Figure 13 – Toggle switch mounted & wired. Figure 14 – Arduino and relay mounted and wired.

Wires can now be run from external components to the enclosure. All of the wires should be run neatly trough the channels of the frame into the enclosure via the strain reliefs. In our case, we found the best way to run the wires was to run all wires pertaining to the head through the right side strain relief, the charge leads run through the bottom strain relief, and everything else runs through the top. The charge leads include both the main charger connections as well as the balance port for the two cells. 3 pin JST-XH male-female balancer cables are used to extend the balance leads outside of the enclosure so that they can be plugged in without taking the enclosure cover off. A female T-style connector is used for the main charge leads for easy and safe connection to the charger. When running the cables from the enclosure to the slave tablet, it is best to run these cables in two separate channels in the frame. This is because one cable is used for charging (high current) and the other cable is used for audio signal (low current). When these two cables are close to each other, the high current cable induces a voltage (electromagnetic noise) on the low current cable, ultimately resulting in unwanted audible noise heard from the speakers. It is for this reason that these two wires should be kept away from each other as much as possible. The wires can be hidden in the channels using the T-slot cover, seen below in Fig. 15.

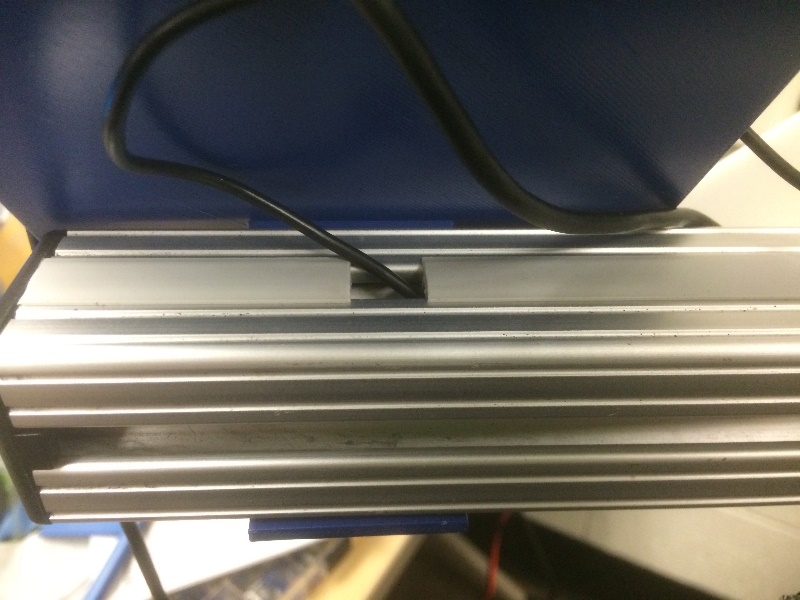
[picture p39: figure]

Figure 15 – T-slot cover used to hide wires.

## Software

With the mechanical and electrical components taken care of, it is finally time to prepare the software to be loaded onto the tablets. The master tablet can be loaded with the SecuroBotMaster application. This app does not require any intervention, but if you would like, there are several different eye options available included in the drawable folder. You can change the code to use these files instead if you wish. The next step is to set up the SecuroBotSlave app. Before this can be loaded, you must first take care of a few preliminary things. You must create an account with mashape.com and purchase a subscription to the SIRI API by pannous, which can be done here:

https://market.mashape.com/pannous/siri/pricing

Next you will have to create a twitter account for your Ada, and then sign in to Twitter’s app management system with your username and password by going here:

https://apps.twitter.com/

Here, you will start a new app and fill out all the required fields. You should see four different keys – Consumer key, Consumer secret, Access token, and Access token secret. You will then take your mashape SIRI key, your four twitter keys, and your twitter username and enter them as the corresponding strings in the Constants.java within the SecuoBotSlave project in Android Studio. Once this is done, you can plug your slave tablet into the computer and press the green play button in Android Studio to load the app onto the tablet.

Now that you have the apps loaded on both tablets, you can install the tablets in their respective places on Ada (master on the head, slave on the arm). If you plan on having Ada reside in a public place with low supervision, it is recommended that you take some security precautions. It is best to set a screen lock, preferably one that is not easy to guess. The other thing you may want to do is to pin the app. This is a feature that was recently built into android which allows for you to lock the screen on a certain app. That way, users can’t purposely or accidentally navigate away from the Ada app. To pin an app, open the app as normal, then click the android menu button and press the green pin icon in the bottom right corner of the app view. To exit the pinned view, press and hold the back and menu buttons and then enter your password. You may also find that the screen dims after a few minutes. One way to keep the brightness on all the time is to download an app called Stay Alive. This app can be set to stay on all the time or turn off after a certain amount of time.

We hope that you enjoyed reading this article and have been inspired to create your own Ada. We look forward to seeing how the world reacts to Ada and be sure to stay connected with UNHcFREG for updates on our research. Please feel free to comment with questions.

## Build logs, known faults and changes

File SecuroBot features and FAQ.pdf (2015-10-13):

Who/what

is

Ada?
- Ada

is

a

cyber

security

educational

animatronic

robot
- Ada

will

be

used

as

a

fun

interactive

way

to

teach

people

about

good

cyber

security
practices,

how

to

keep

yourself

safe

while

online,

and

show

the

new

trends

in

the

cyber
security

field.

Why

name

it

Ada?
- Because

this

robot

is

basically

a

computer

teaching

people

about

computer

safety,

and
speaks

with

a

female

voice,

we

found

it

fitting

to

name

it

after

the

first

woman

in
computer

science

– Ada

Lovelace.

What

can

Ada

do?
- Ada

can

sense

a

person

approaching

her

and

will

react

by

greeting

them
- Users

can

then

choose

from

one

of

8

different

cyber

security

related

activities:
- Show

an

article
- Take

a

quiz
- Tell

a

joke
- Take

and

tweet

a

picture

with

Ada
- Read

a

tweet
- See

if

you

have

been

hacked
- Read

an

RSS

feed
- Say

a

tip
- You

can

also

start

a

conversation

with

Ada

by

pressing

the

microphone

button,

and

she
answers

back!

Where

did

this

idea

come

from?
- This

idea

began

as

a

term

project

for

the

Intro

to

Computer

Security

course

here

at
UNH,

with

the

original

plans

having

much

fewer

features.

With

a

little

help

and

a

lot

of
patience,

Ada

has

grown

into

the

fully

functional

robot

she

is

today.

How

does

Ada

work?
- Ada’s

brain

is

an

android

tablet

running

a

custom

application.

The

application

manages
her

interaction

with

people,

the

things

she

says,

and

the

way

she

moves,

just

like

a

real
brain.
- The

app

forms

a

Bluetooth

connection

to

the

hardware

to

control

its

head

movements
and

read

its

motion

sensor.
- Ada

gets

all

her

knowledge

on

cyber

security

from

her

very

own

Twitter

account
(@Ada_SecuroBot)

which

is

updated

by

the

brainiacs

of

the

UNH

Cyber

Forensics,
Research

and

Education

Group (UNHcFREG)

with

tips,

articles,

RSS

feeds,

retweets,
jokes,

and

more.
- Ada

is

an

artificially

intelligent

robot,

capable

of

carrying

out

a

conversation

with
someone

by

utilizing

an

artificial

intelligence

API,

similar

to

Apple’s

™

Siri.
- Ada’s

body

was

designed

in

CAD

with

several

parts

that

were

3D

printed.

How

can

I

get

an

Ada?
- All

of

the

CAD,

software,

documentation,

and

bill

of

materials

for

this

project

will

soon
be

released

open

source

for

all

who

are

interested.

Anyone

and

everyone

will

be

able

to
download

the

entire

Ada

project

completely

free.

What

does

the

future

look

like

for

Ada?
- It

is

our

hope

that

schools

and

universities

will

take

on

this

project,

build

it

with

their
students,

using

it

as

an

educational

tool

both

during

the

build

process

and

long

after.
- We

hope

to

collaborate

with

other

schools

and

universities

to

share

statistics

from
quizzes

to

be

able

to

better

assess

where

improvements

should

be

made

in

cyber
security

education

in

the

future.
- Connect

with

schools

to

share

articles,

RSS

feeds,

tips

and

more.
- Take

Ada

on

the

road

to

local

schools

to

educate

young

students

on

cyber

security

in

a
fun

and

engaging

way.
- Establish

a

developer

base

of

talented

project

contributors

to

make

improvements

to
the

system

and

its

functionalities.

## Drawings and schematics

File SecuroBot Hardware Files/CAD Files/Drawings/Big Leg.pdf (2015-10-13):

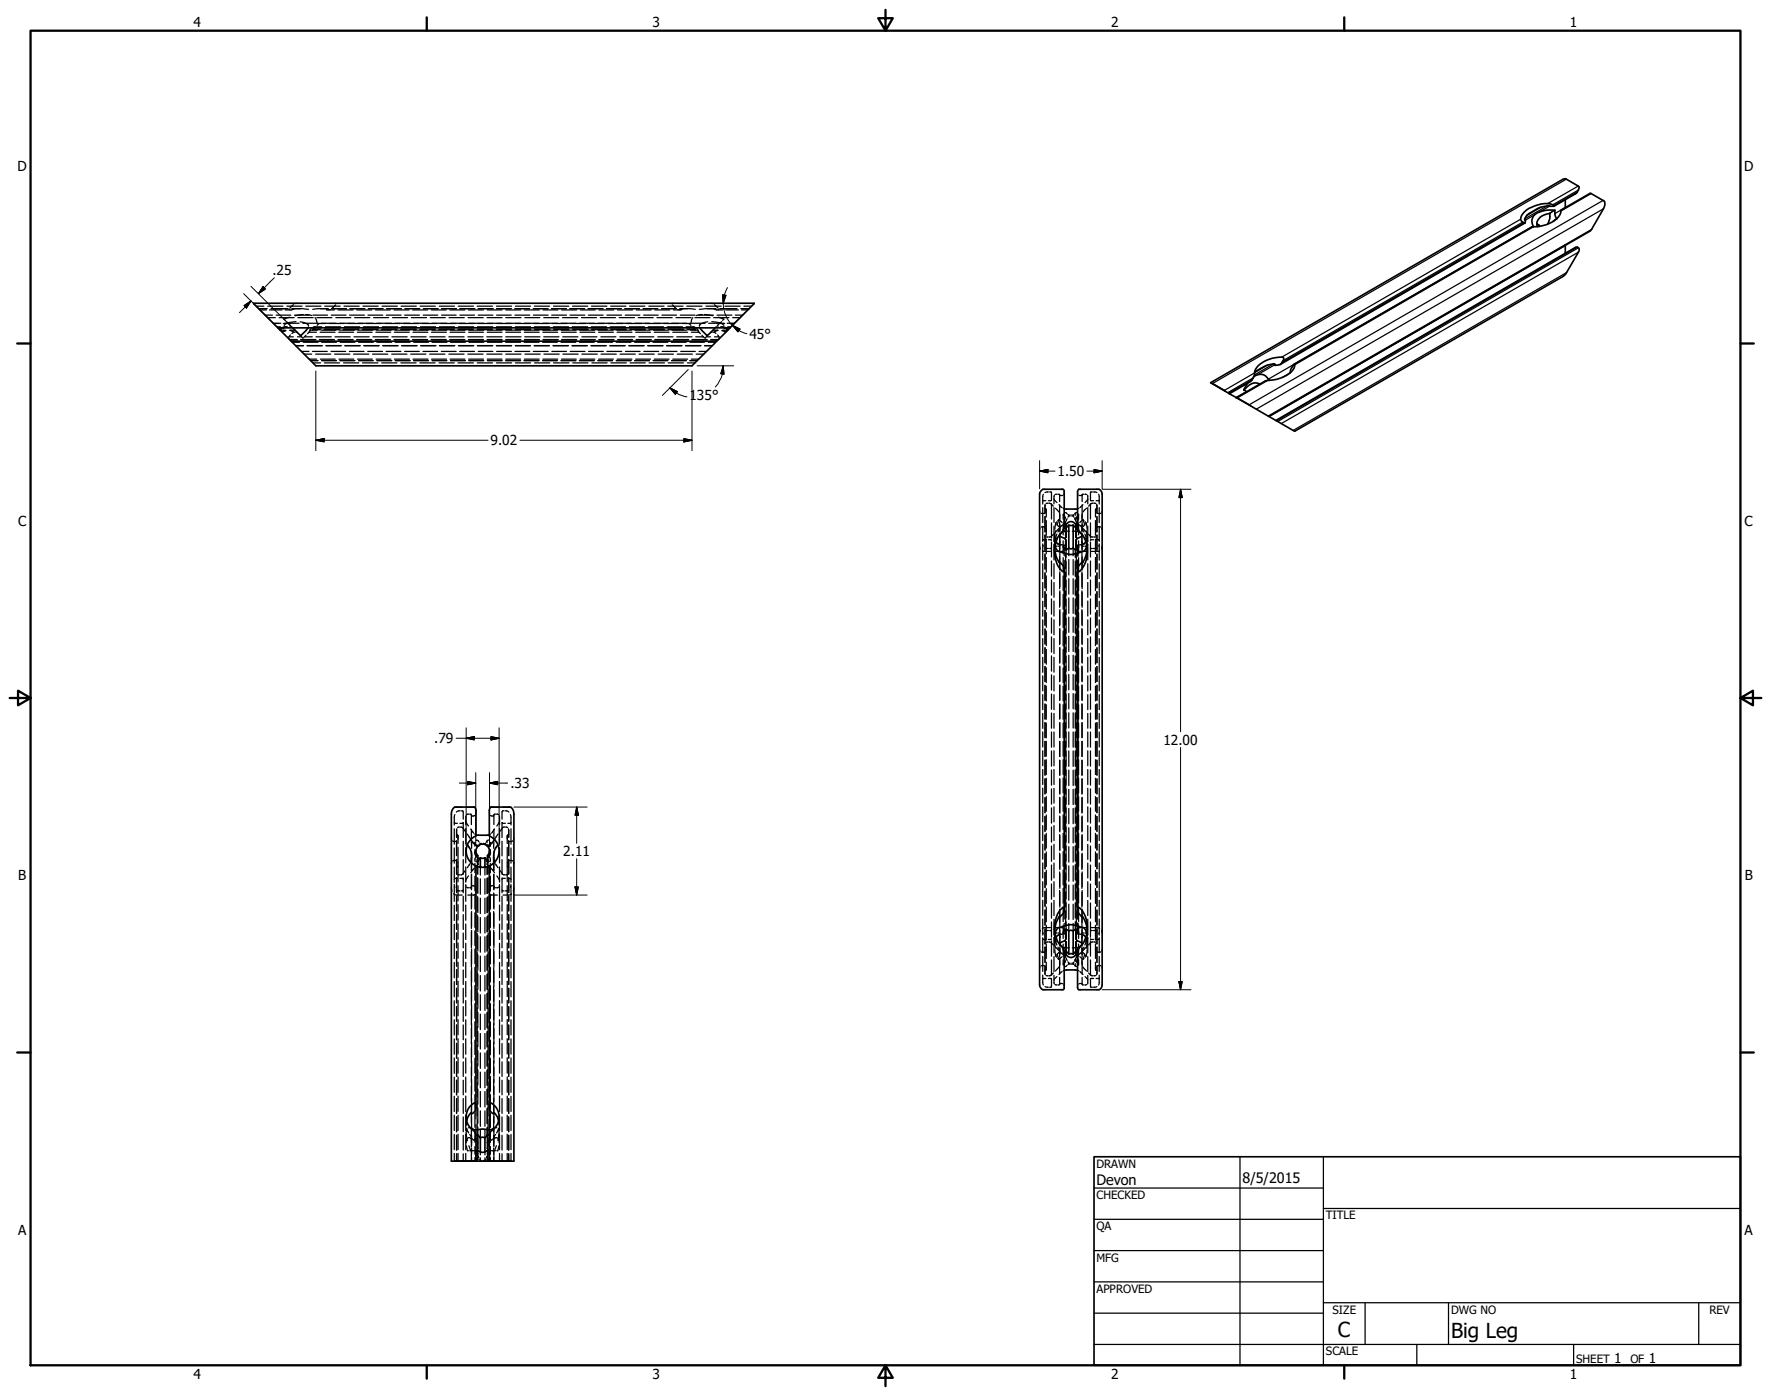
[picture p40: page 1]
SHEET 1 OF 1; DRAWN; CHECKED; MFG; APPROVED; Devon; DWG NO Big Leg; TITLE; SIZE C; SCALE; REV

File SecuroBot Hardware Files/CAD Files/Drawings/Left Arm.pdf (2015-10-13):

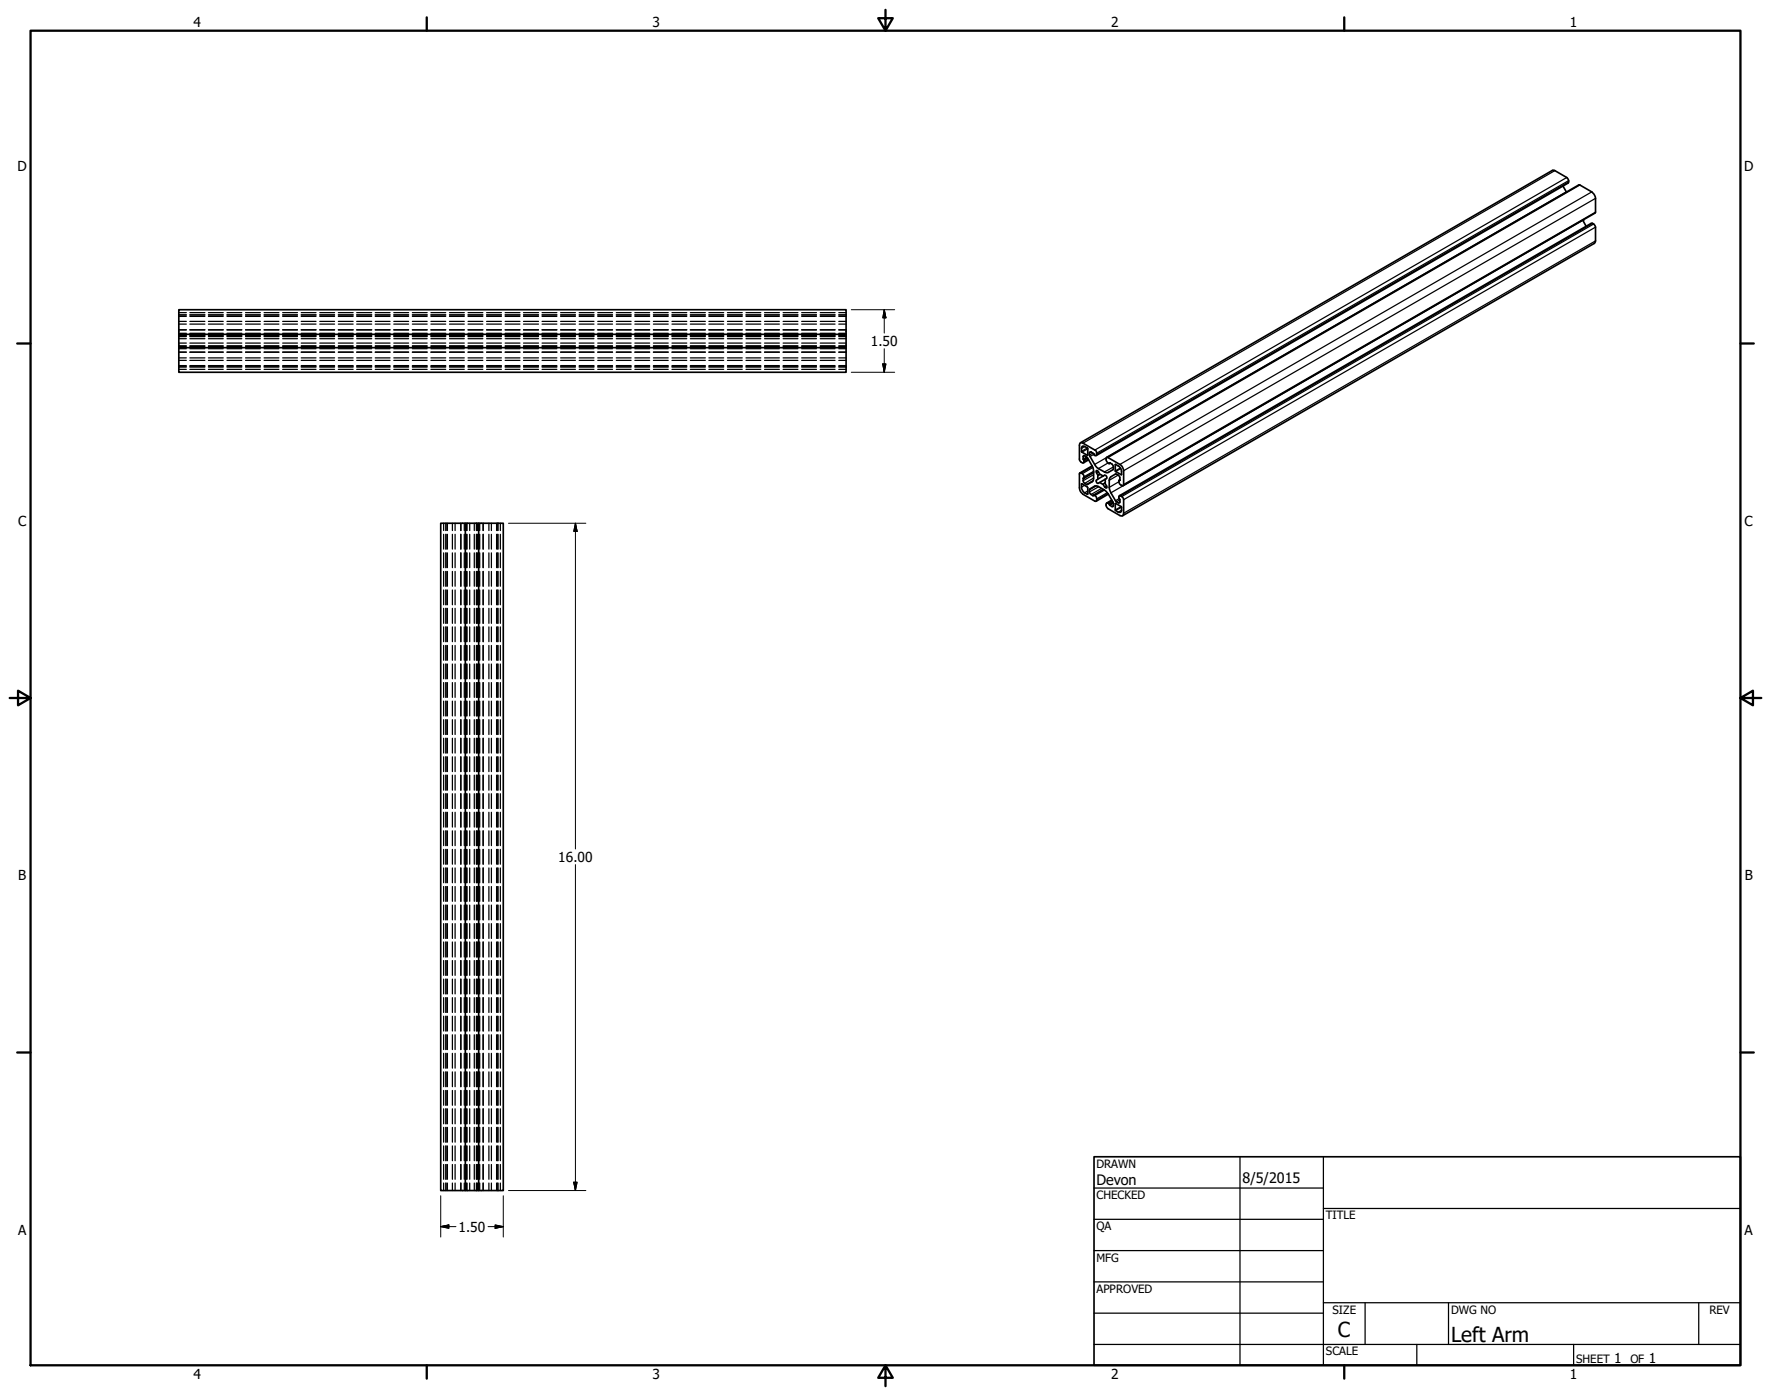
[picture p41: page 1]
SHEET 1 OF 1; DRAWN; CHECKED; MFG; APPROVED; Devon; DWG NO Left Arm; TITLE; SIZE C; SCALE; REV

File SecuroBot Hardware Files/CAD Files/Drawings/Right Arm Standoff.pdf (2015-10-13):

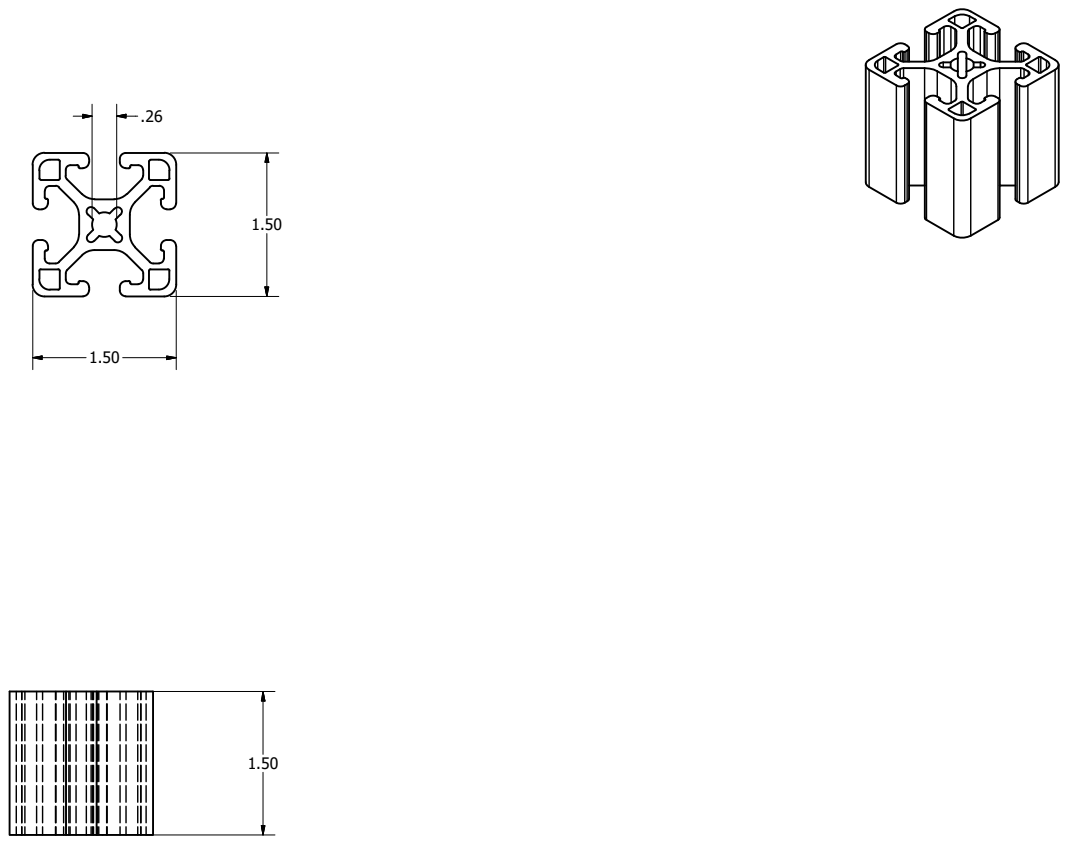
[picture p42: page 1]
SHEET 1 OF 1; DRAWN; CHECKED; MFG; APPROVED; Devon; TITLE; SIZE C; SCALE; REV

DWG NO
Right Arm Standoff

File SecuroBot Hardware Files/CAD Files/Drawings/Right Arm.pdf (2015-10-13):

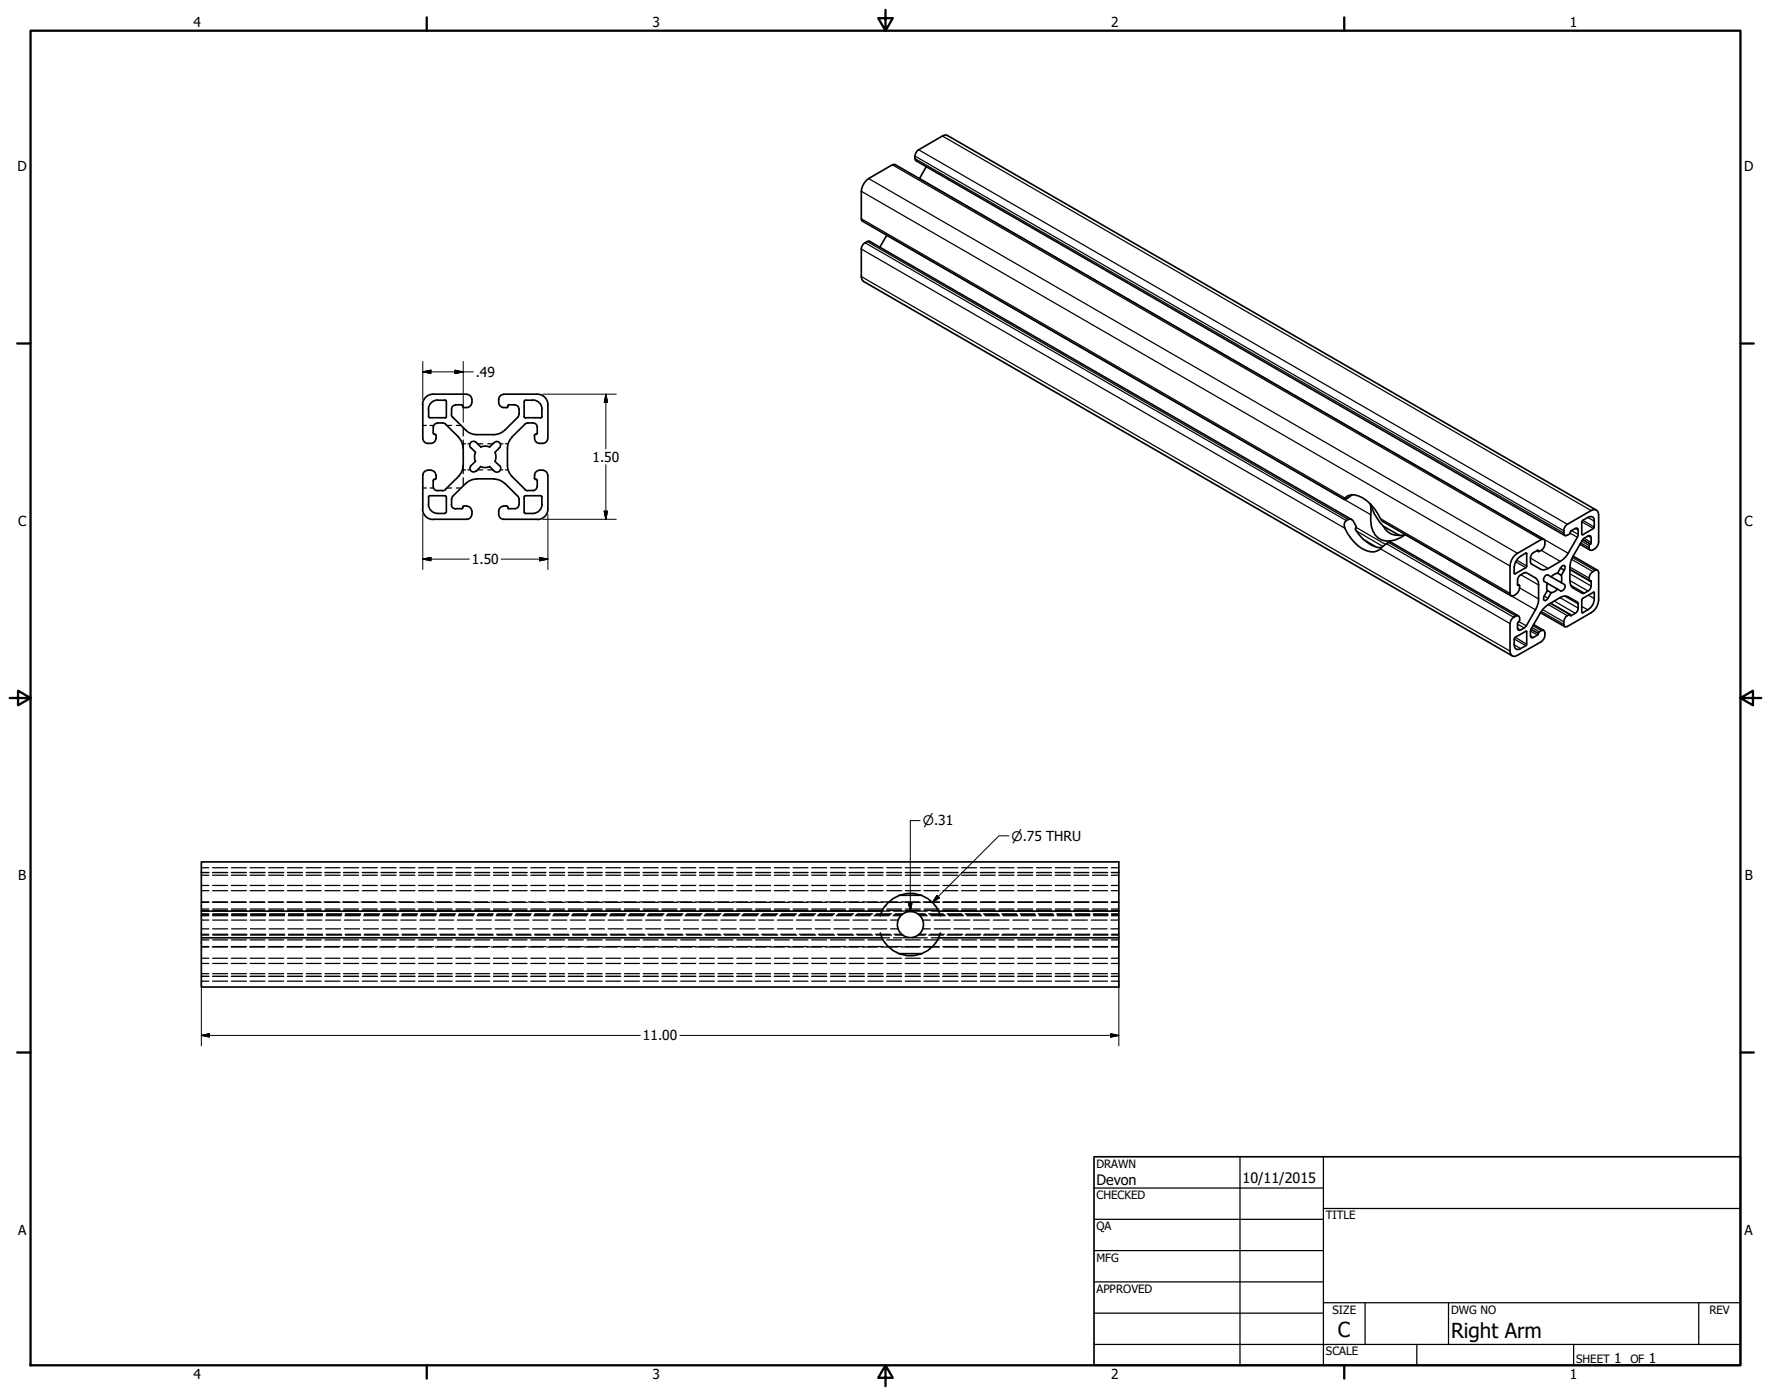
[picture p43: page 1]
SHEET 1 OF 1; DRAWN; CHECKED; MFG; APPROVED; Devon; DWG NO Right Arm; TITLE; SIZE C; SCALE; REV; P.75 THRU

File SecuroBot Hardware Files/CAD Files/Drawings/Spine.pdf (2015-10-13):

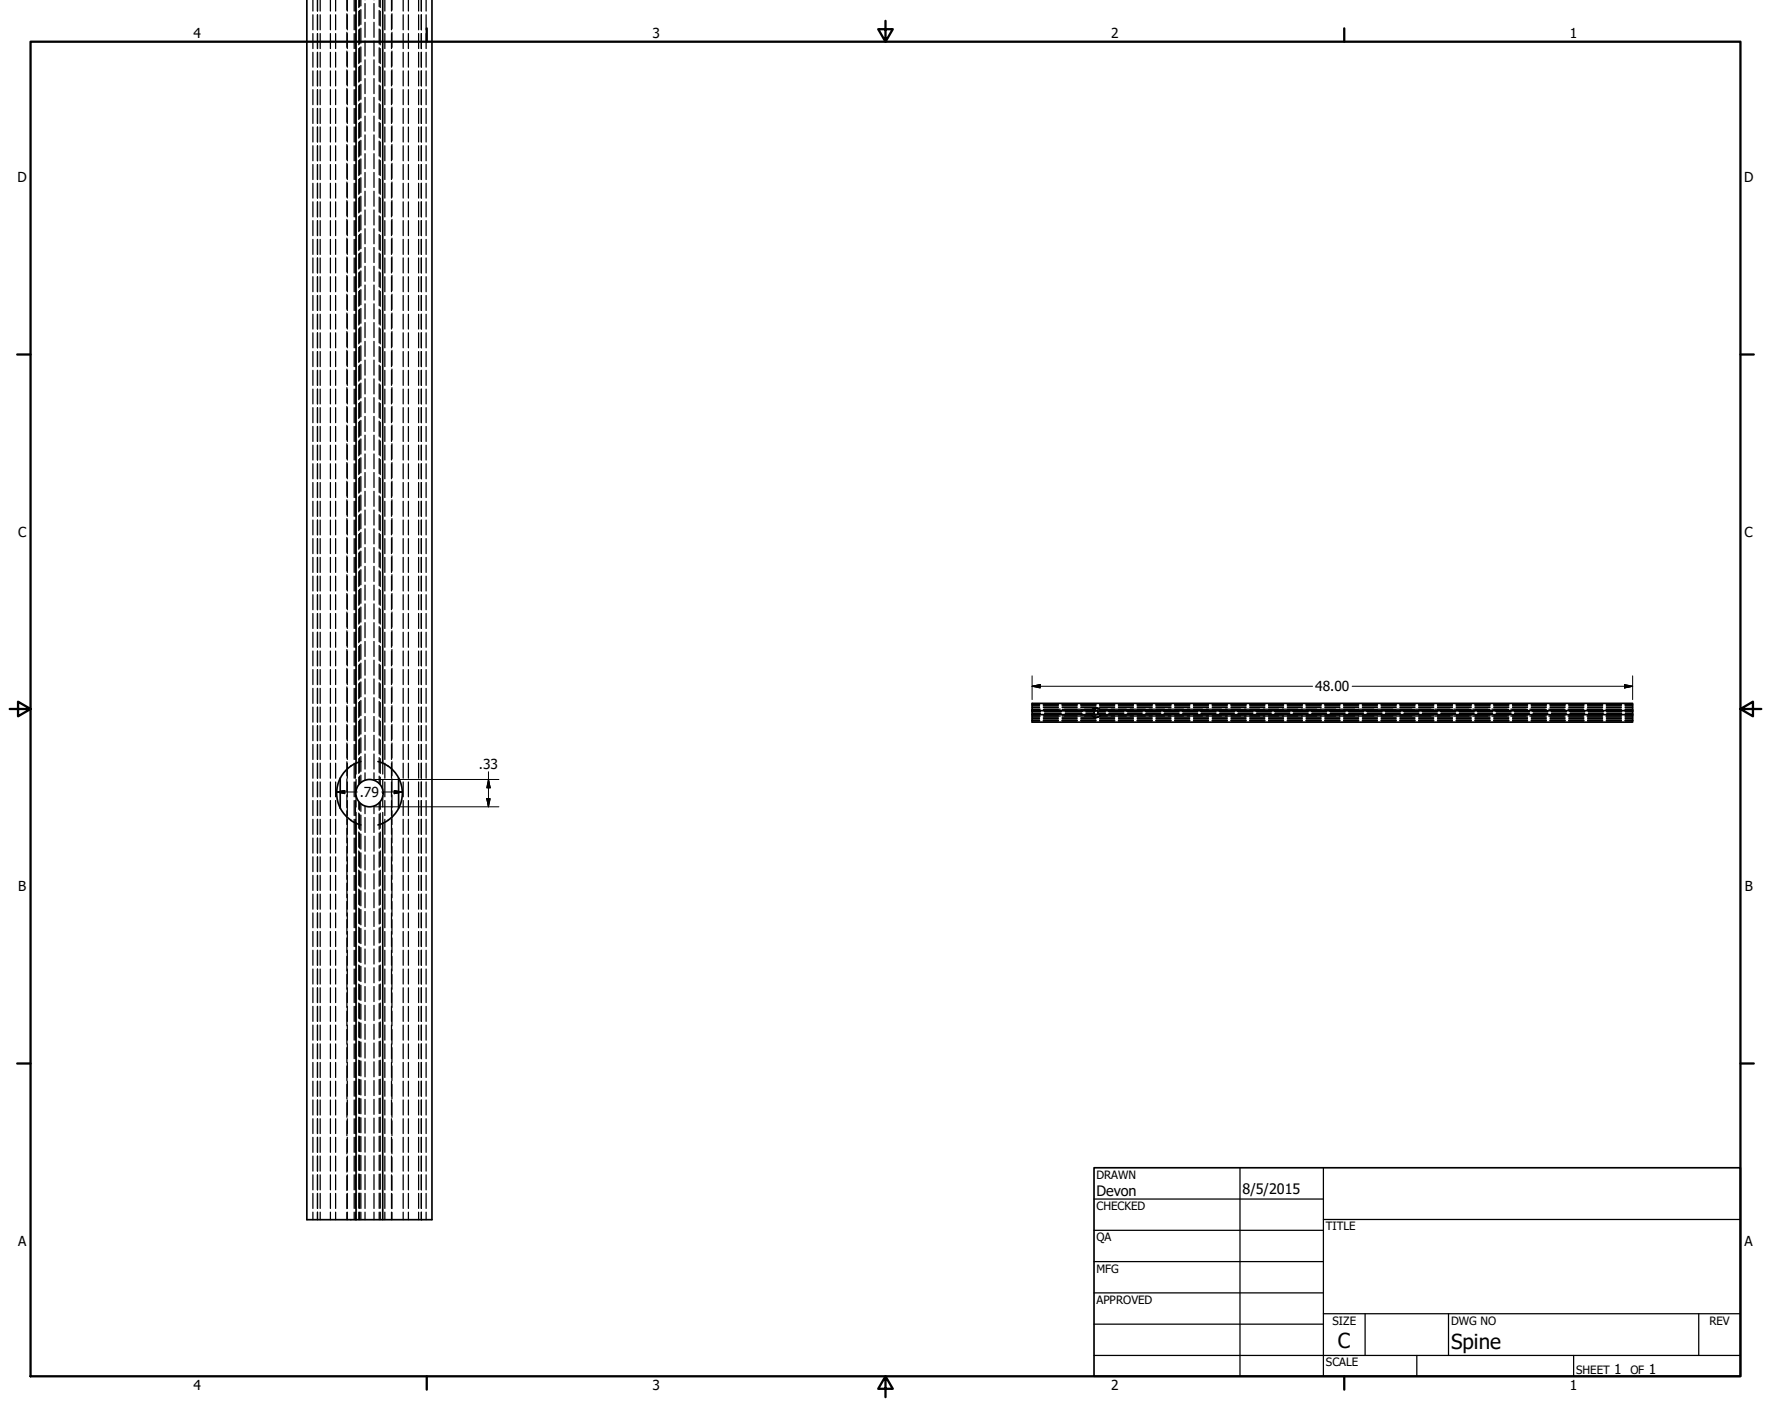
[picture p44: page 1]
SHEET 1 OF 1; DRAWN; CHECKED; MFG; APPROVED; Devon; DWG NO Spine; TITLE; SIZE C; SCALE; REV

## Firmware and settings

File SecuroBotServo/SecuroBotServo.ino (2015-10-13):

/* Sweep
 by BARRAGAN <http://barraganstudio.com> 
 This example code is in the public domain.

 modified 8 Nov 2013
 by Scott Fitzgerald
 http://www.arduino.cc/en/Tutorial/Sweep
*/ 

#include <Servo.h> 
 
Servo myservo;  // create servo object to control a servo 
                // twelve servo objects can be created on most boards

int maxPos = 150;
int midPos = 85;
int minPos = 20;
int initPos = midPos;
int pos = minPos;    // variable to store the servo position 
int relayPin = 7;

void setup() 
{ 
  myservo.attach(9);  // attaches the servo on pin 9 to the servo object 
  pinMode(relayPin, OUTPUT);
  initServo(initPos);
  Serial.begin(9600);
  delay(3000);
  digitalWrite(relayPin, HIGH);
} 
 
void loop() 
{
  if(Serial.available()) {
    int readVal = Serial.read();
    Serial.print("Serial Value Read: ");
    Serial.println(readVal);
    switch(readVal) {
      case 1: 
          moveServo(minPos);
          break;
      case 2: 
          moveServo(midPos);
          break;
      case 3: 
          moveServo(maxPos);
          break;
      default: 
          //moveServo(midPos);
          break;
    }
  }
} 

void moveServo(int newPos) {
  if(newPos>pos) {  //fwd
    for(; pos <= newPos; pos += 1) // goes from 0 degrees to 180 degrees 
    {                                  // in steps of 1 degree 
      myservo.write(pos);              // tell servo to go to position in variable 'pos' 
      delay(15);                       // waits 15ms for the servo to reach the position 
    }
    delay(500);
  }
  else if(newPos<pos) { //rev
    for(; pos >= newPos; pos -= 1)     // goes from 180 degrees to 0 degrees 
    {                                
      myservo.write(pos);              // tell servo to go to position in variable 'pos' 
      delay(15);                       // waits 15ms for the servo to reach the position 
    }
    delay(500);
  }
  serialResponse();
}

void initServo(int start) {
  myservo.write(start);
  delay(1500);
}

void serialResponse() {
  Serial.write(0x01);
}

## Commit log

2015-10-13 Project Ada initial commit
    [1 inch extrusion base ipt.0003.ipt, 1 inch extrusion base ipt.ipt, 1 inch extrusion base.step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]
2015-10-13 Added Arduino code
